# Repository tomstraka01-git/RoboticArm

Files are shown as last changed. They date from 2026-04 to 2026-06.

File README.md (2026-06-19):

# Robotic Arm
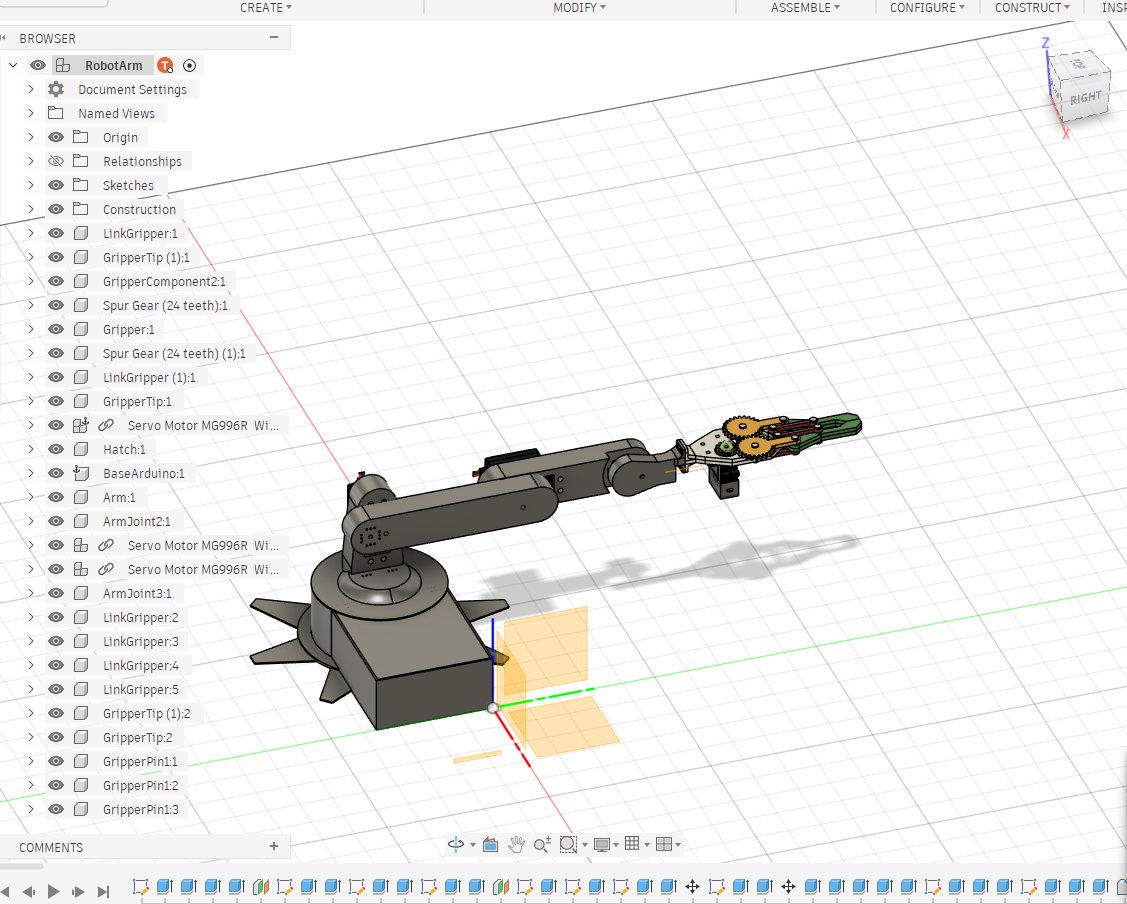
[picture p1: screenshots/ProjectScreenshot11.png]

Robotic arm is a  project about making my own robotic arm from scratch. I designed the arm from scratch and i plan to 3D print the file. Both firmware codes are written by me. The C++ code will run on  microcontroller, i will be using pico 2. The python code can be run on any computer wich can run python files. 

## Operation
First assemble the arm and try to set the servos in 90 degrees position. Then compile the code and wire everything together. After that run the python code and connnect the microcontroller via usb to your computer. Then use the python code to operate it, send signals, set position and record position. The main inverse and forward kinematics run on the pc, the c++ microcontroller code just recieves the serial commands. It uses cosine ease when animating through the listbox to make the movement seems smooth, moves nonlinearly.

### Keybinds
Use keybinds to control the robotic arm easily.
```
[t]: increments the time by 0.5 seconds
[q]: closes the serial port and GUI
[l]: loads animation
[s]: saves animation
[space]: animates smoothly through loaded positions or angles
[r]: records the current position onto the listbox
```
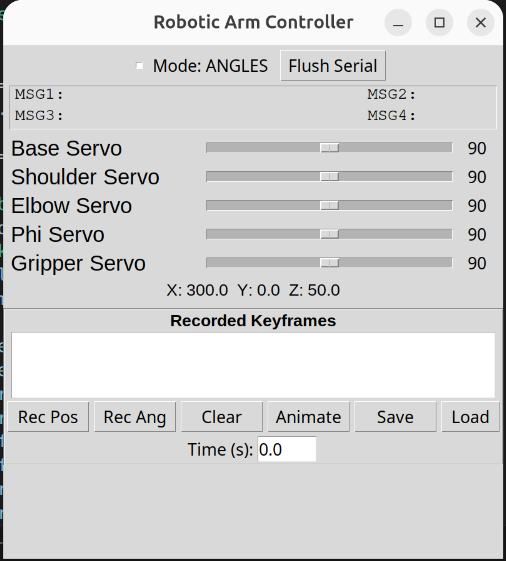
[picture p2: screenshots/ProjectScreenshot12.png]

## What can it do?
You can set positions manually, record and play animations, pick up objects, use it to help you in your everyday life.

## Circuit
The circuit consists of a microcontroller, can be any but i chose pico 2. A PCA9685 servo driver servos, exteral power source and i pcb i will use from my other project. Connect servos to the pcb pins, and connect gnd to gnd and 5V to pcb 5V. Connect signal pins from pcb pins to PCA9685 signal pins. Connect sda scl and power pins from pico 2 to PCA9685. Then upload the code and turn on the power supply. The power supply should be able to handle around 5v 10 amps for safety. The pcb connects the microcontroller, has the adc voltage dividers, output pins for servos, etc. It connects everything together and makes it simplier. It also has some features i am not using like the fans or the adc, but are in the robotic dog project.

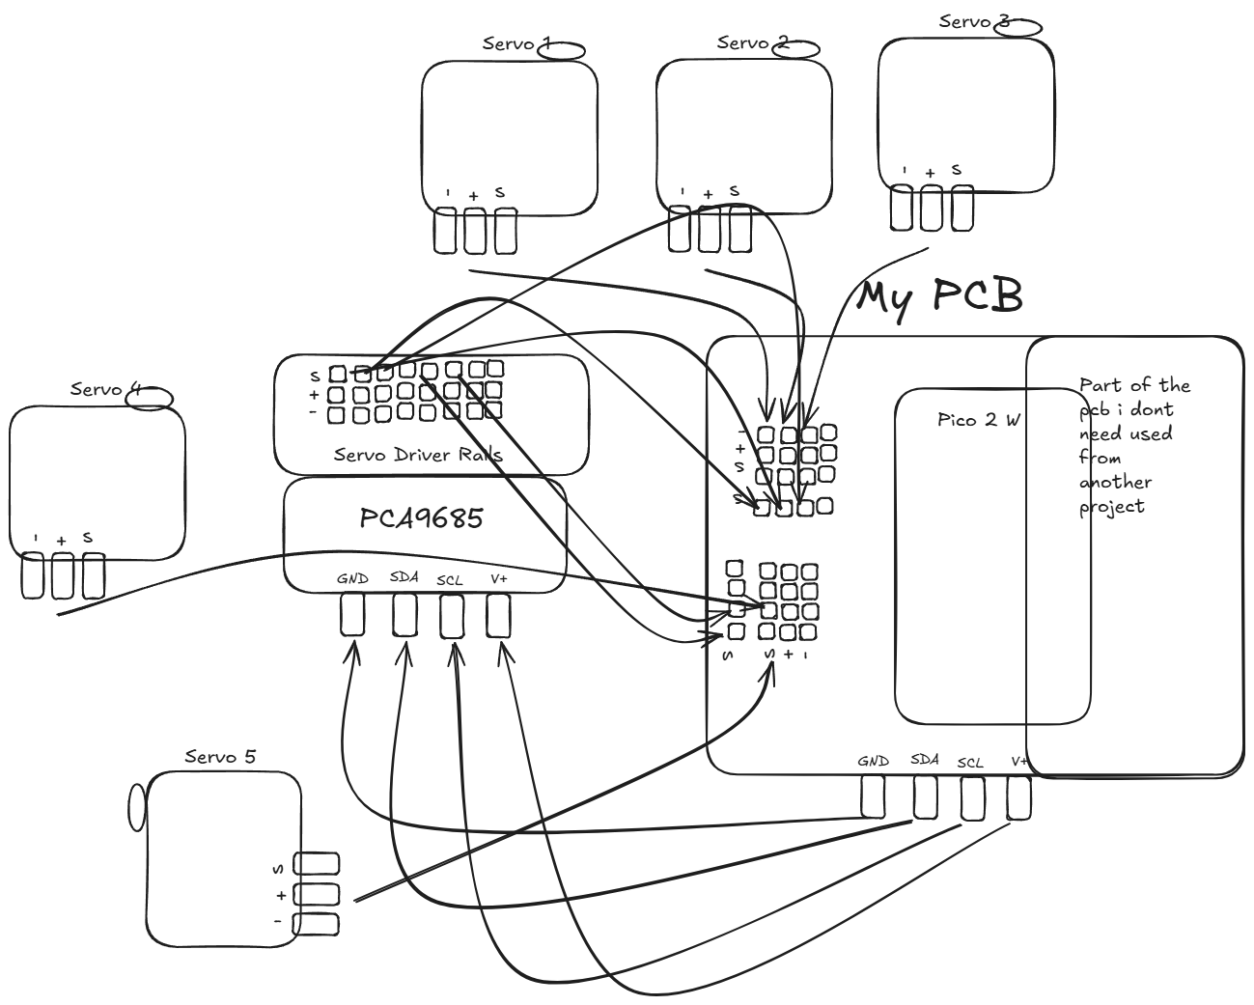
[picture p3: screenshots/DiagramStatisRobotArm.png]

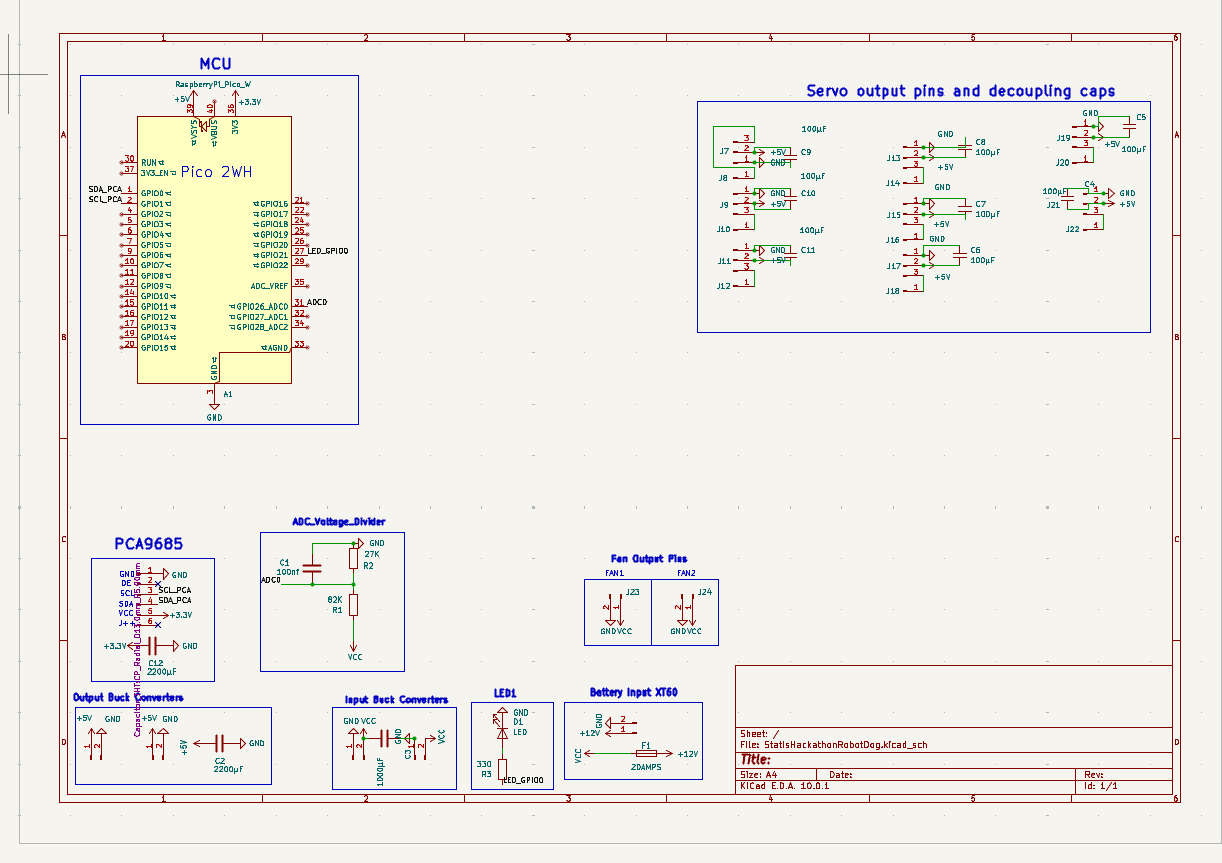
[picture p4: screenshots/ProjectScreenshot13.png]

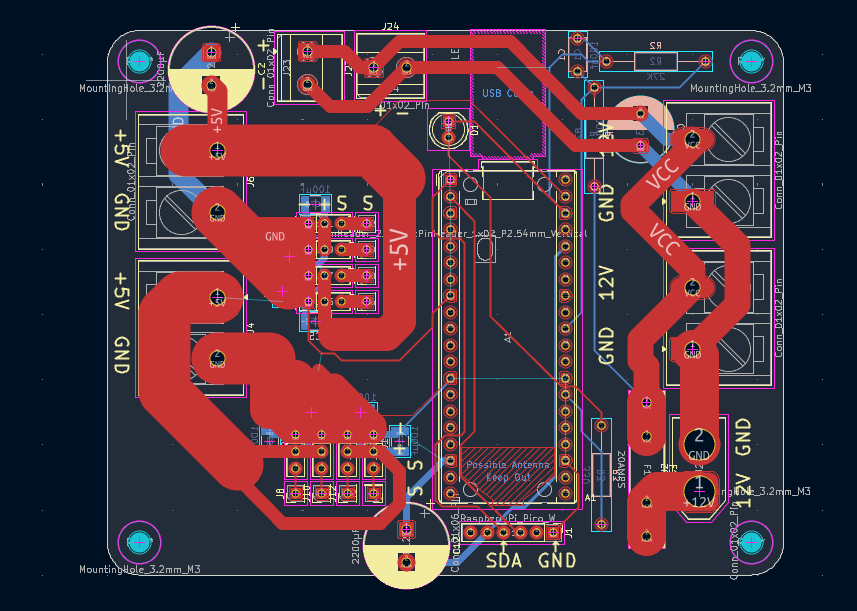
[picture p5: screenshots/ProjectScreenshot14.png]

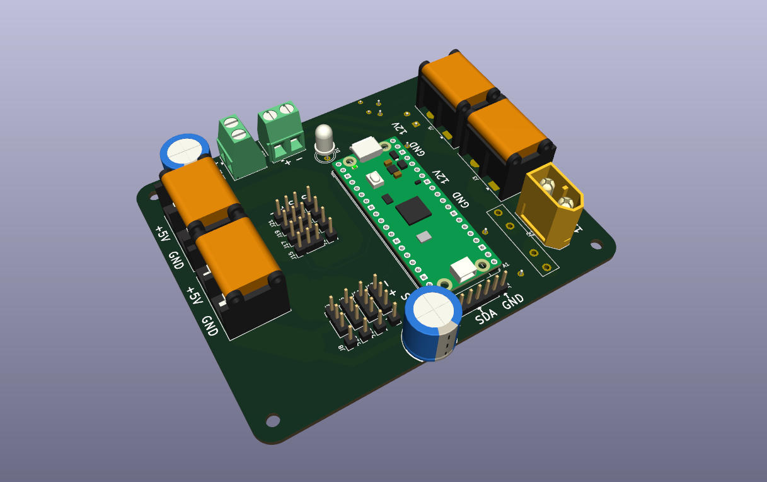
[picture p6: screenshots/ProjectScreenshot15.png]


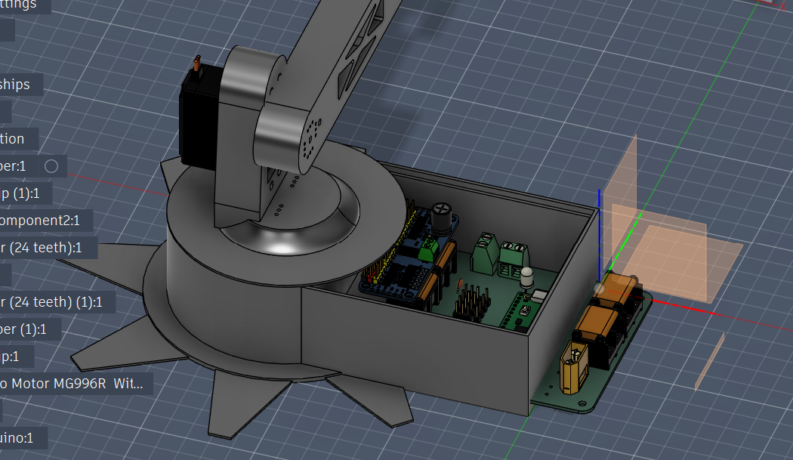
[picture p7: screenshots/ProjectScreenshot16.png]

Here you can see how the pcb will fit into the assembly, the red lines indicate where it will be cut, to save space and remove features from another project i dont need.
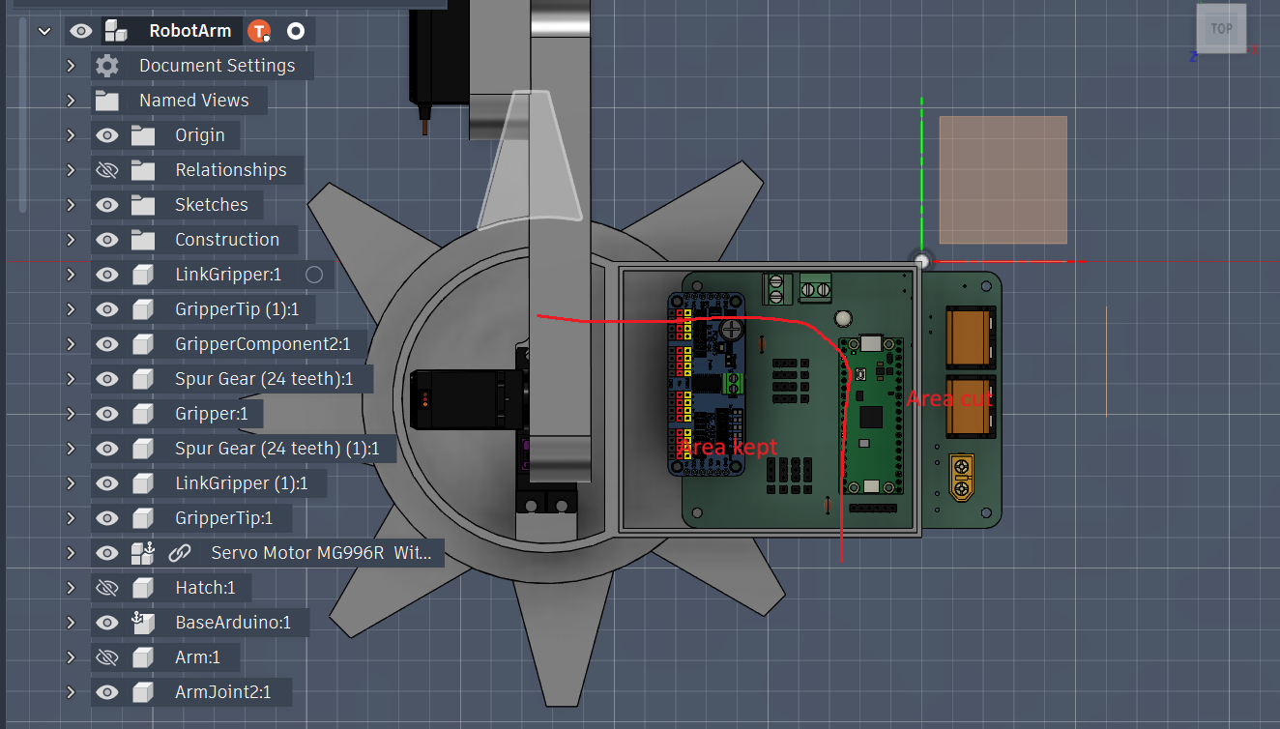
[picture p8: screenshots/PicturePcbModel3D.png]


## How to print?
If you want to replicate the project, you need to buy simillar servos, use some i2c pwm generation module and some circuit to distribute the power. For printing downooad the 3d print file, and use a 3d printer, that has over 400mm print surface. I want to use pla, because it is cheap and okay for my project. You can use other filaments if you want. For my printer, Prusa XL, the slicer says that it would take 22 hours to print and 300 grams to print. Use any microcontroller wich has i2c and serial communication, upload the code and connect it via usb to pc running the python file. Then it should work.

## Why?
Why would i want to build this arm? Because it is a great learning oppurtunity that can teach me many new things. It is also a challange for me, because it is one of my first big projects. I also need a small assistant to help me move things around my desk.



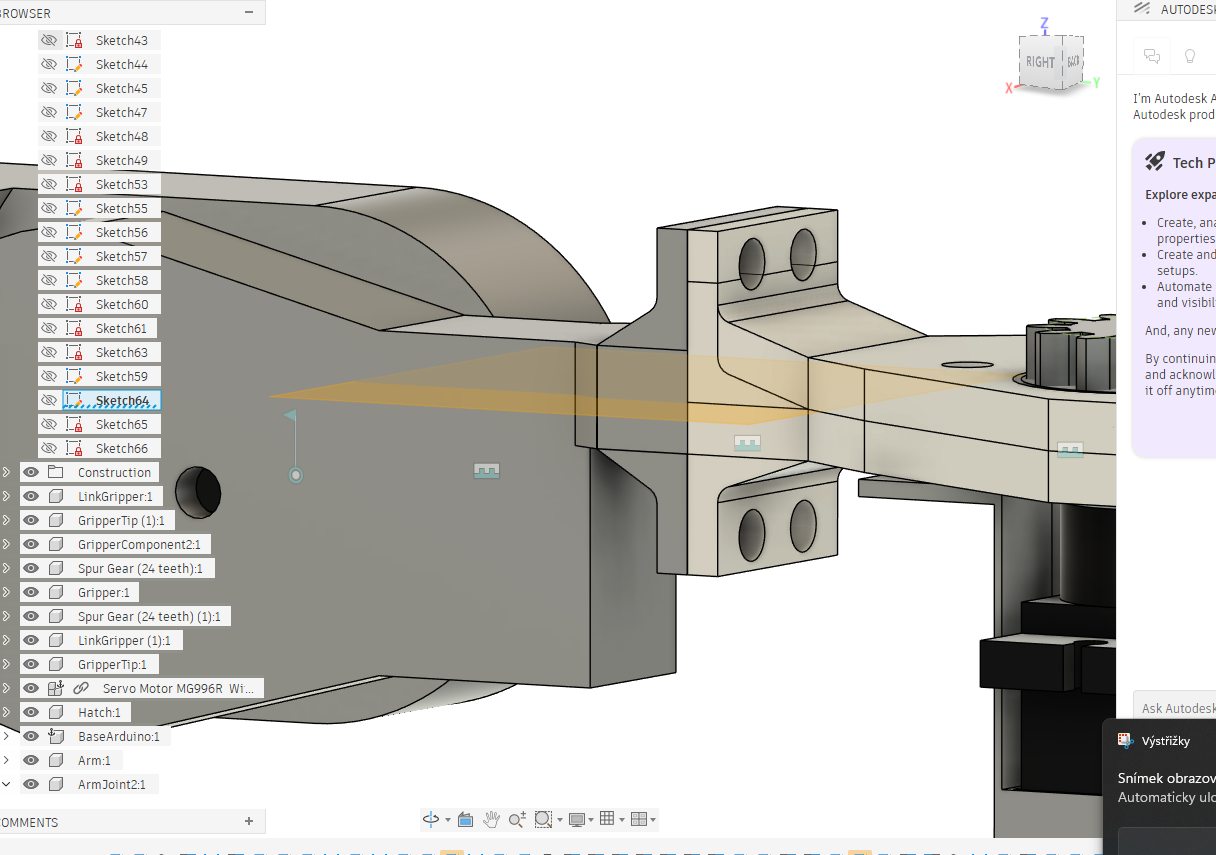
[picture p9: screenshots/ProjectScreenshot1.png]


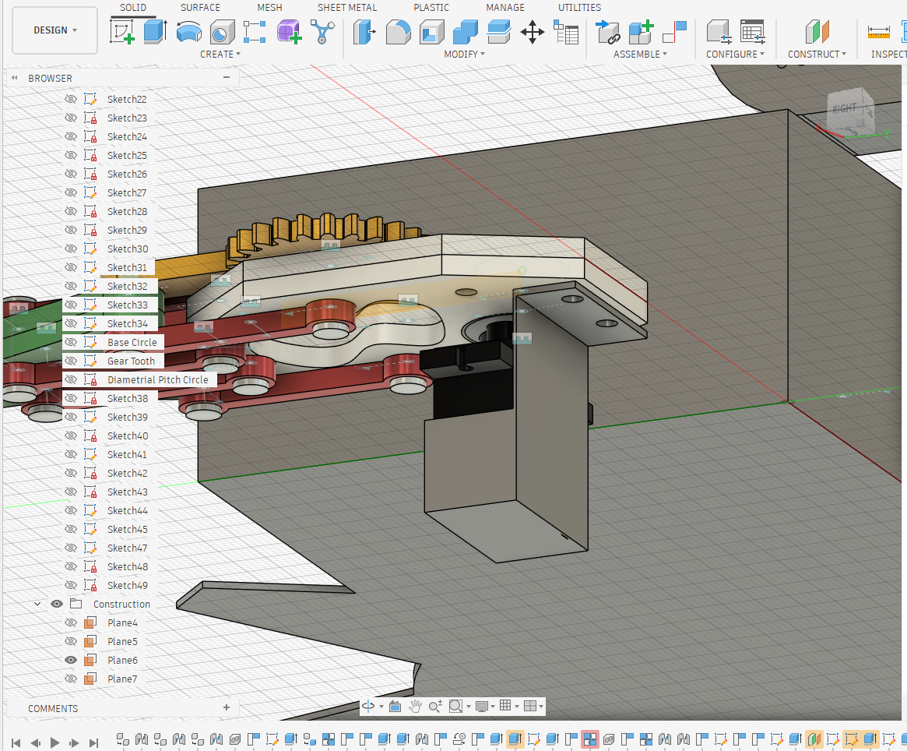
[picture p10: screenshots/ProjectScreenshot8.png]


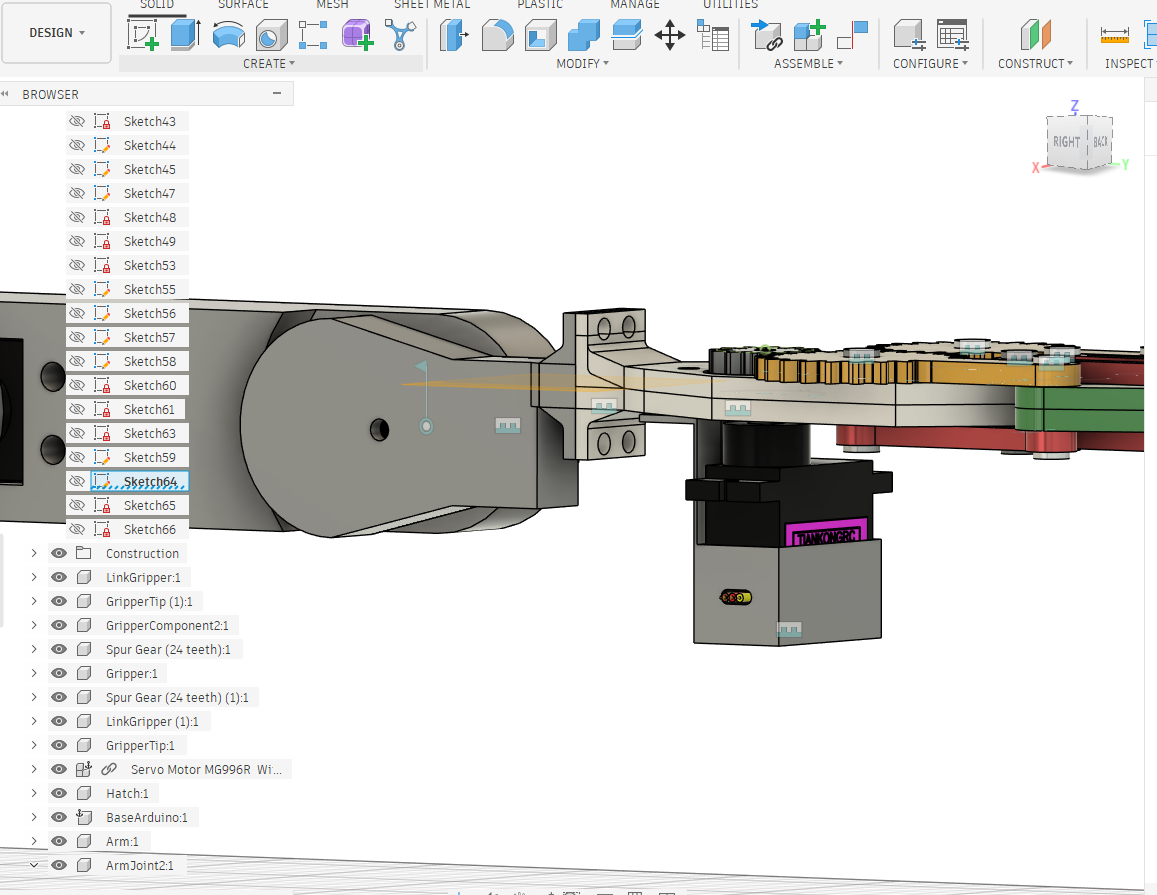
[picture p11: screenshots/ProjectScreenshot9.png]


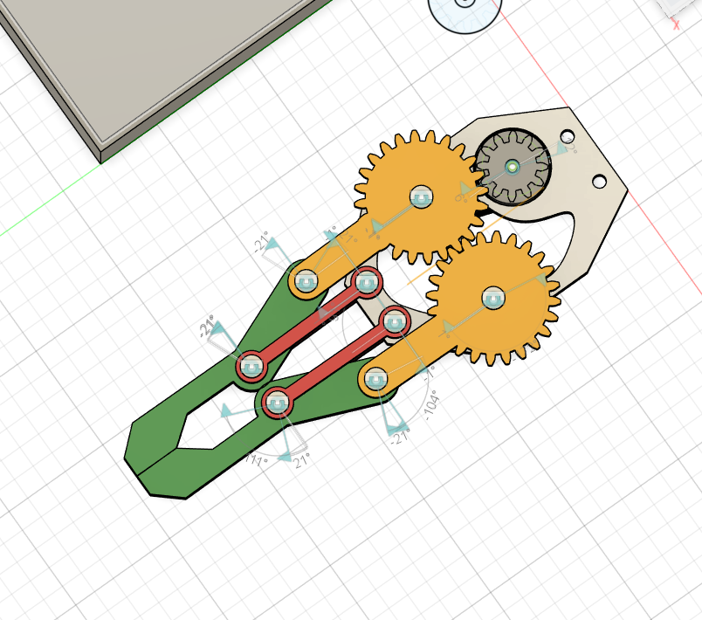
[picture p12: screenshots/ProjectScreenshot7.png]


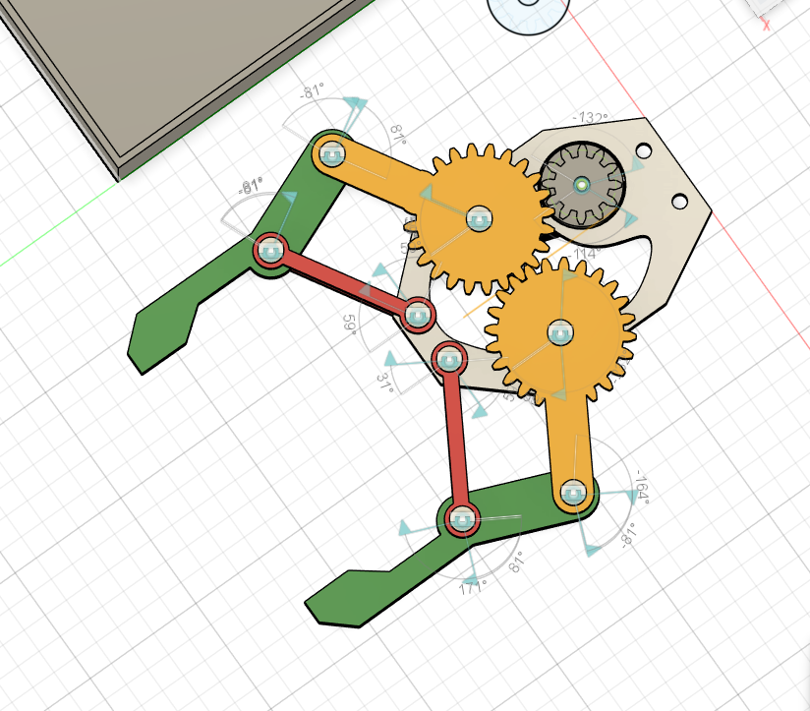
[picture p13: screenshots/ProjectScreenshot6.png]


### Bill of Materials (BOM)

| Name | Purpose | Quantity | Total Cost (USD) | Link | Distributor |
|:---|:---|:---:|:---:|:---|:---|
| Servo 30 cm connector cable extension Male - Female | Cable extension for servo so i can connect it to power and microcontroller when the cable is not long enough to reach it. | 2 | $4.68 | [Link](https://rpishop.cz/servomotory/2878-servo-30-cm-propojka-samec-samice.html) | rpishop.cz |
| Raspberry Pico 2 WH | It is the brain of the robotic arm, will be used to control the servos and if it works compute angles using inverse kynematic for the servos. | 1 | $10.98 | [Link](https://rpishop.cz/590613/raspberry-pico-2-wh/) | rpishop.cz |
| Professional Lab - PLA+ Filament - black(1,75 mm, 1 kg) | It is the filment i will use to print the robotic arm fusion 360 model | 1 | $10.80 | [Link](https://rpishop.cz/616058/professional-lab-pla-plus-cerny/) | rpishop.cz |
| Servo motor MG996R 13 kg, 180° | Motors of the arm, will rotate the joints | 3 | $18.60 | [Link](https://rpishop.cz/641352/servo-mg996r-13-kg/) | rpishop.cz |
| **Total** | | | **$45.06** | | |

Note: PCA9685 I2C driver and power supply were reused from previous projects / already owned, $0 cost.

Made by Tomáš Straka for Statis Hackathon by hackclub.

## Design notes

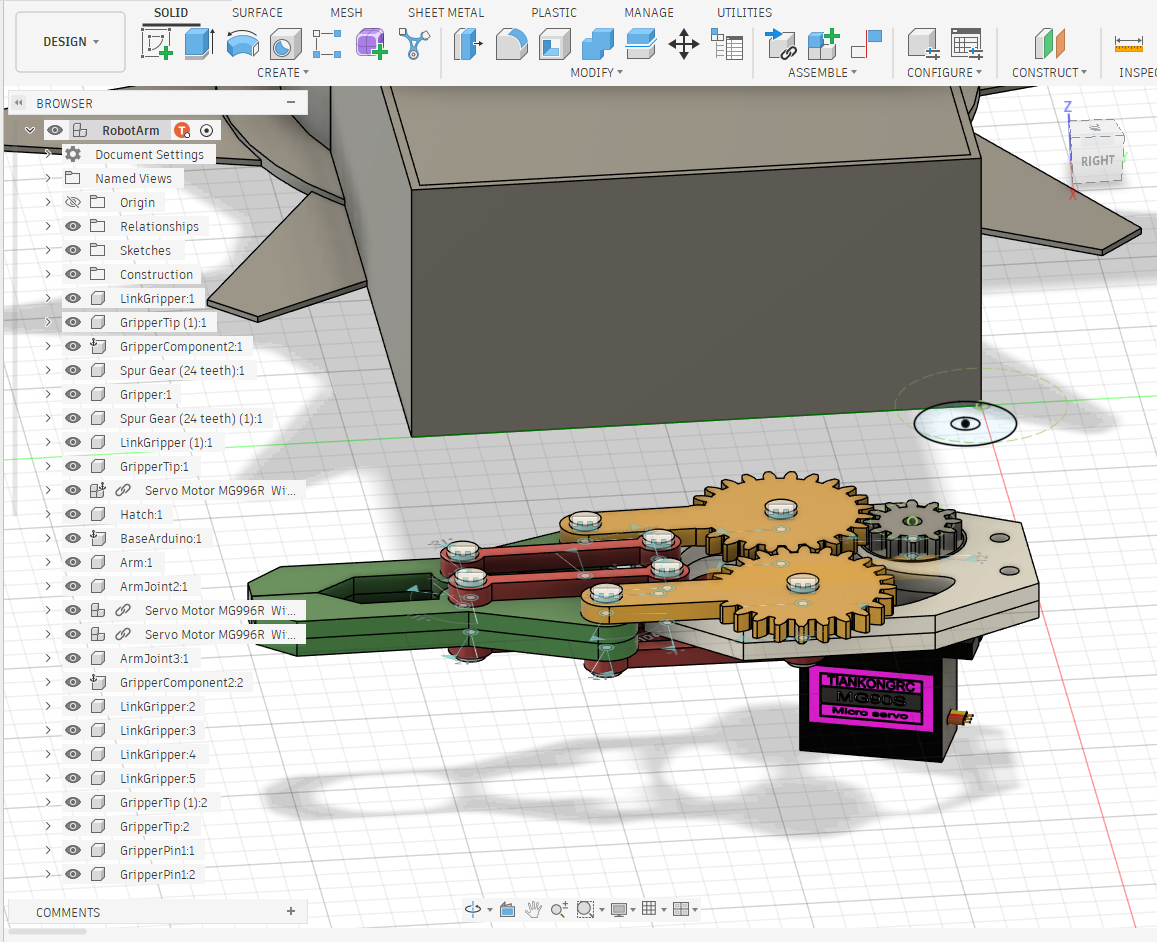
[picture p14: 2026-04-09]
screenshots/ProjectScreenshot5.png

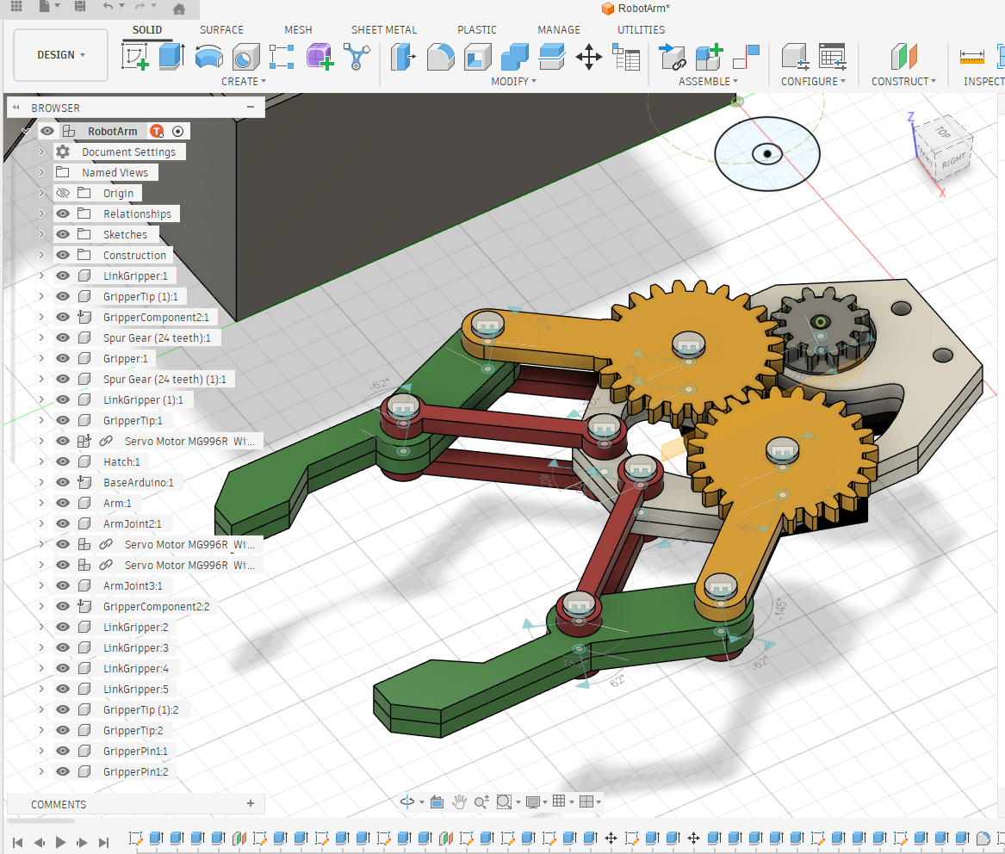
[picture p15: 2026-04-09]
screenshots/ProjectScreenshot4.png

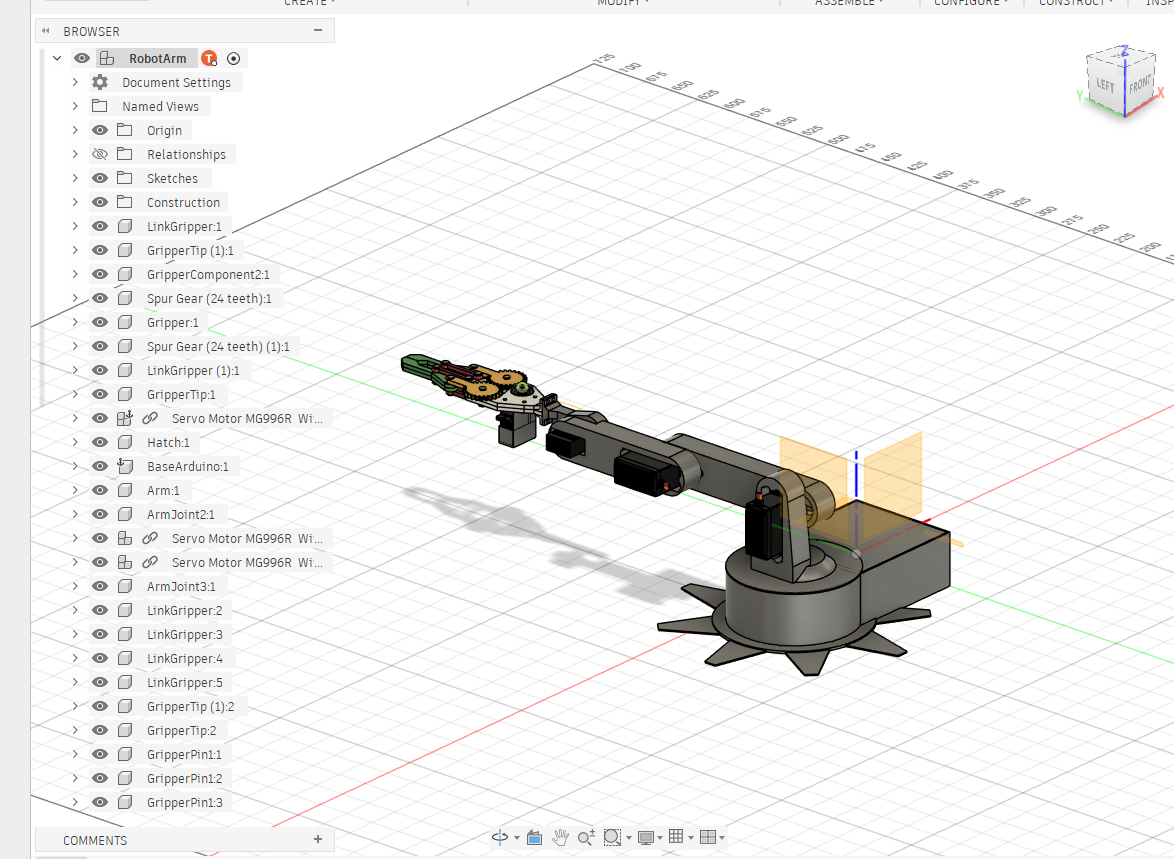
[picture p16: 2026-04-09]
screenshots/ProjectScreenshot10.png

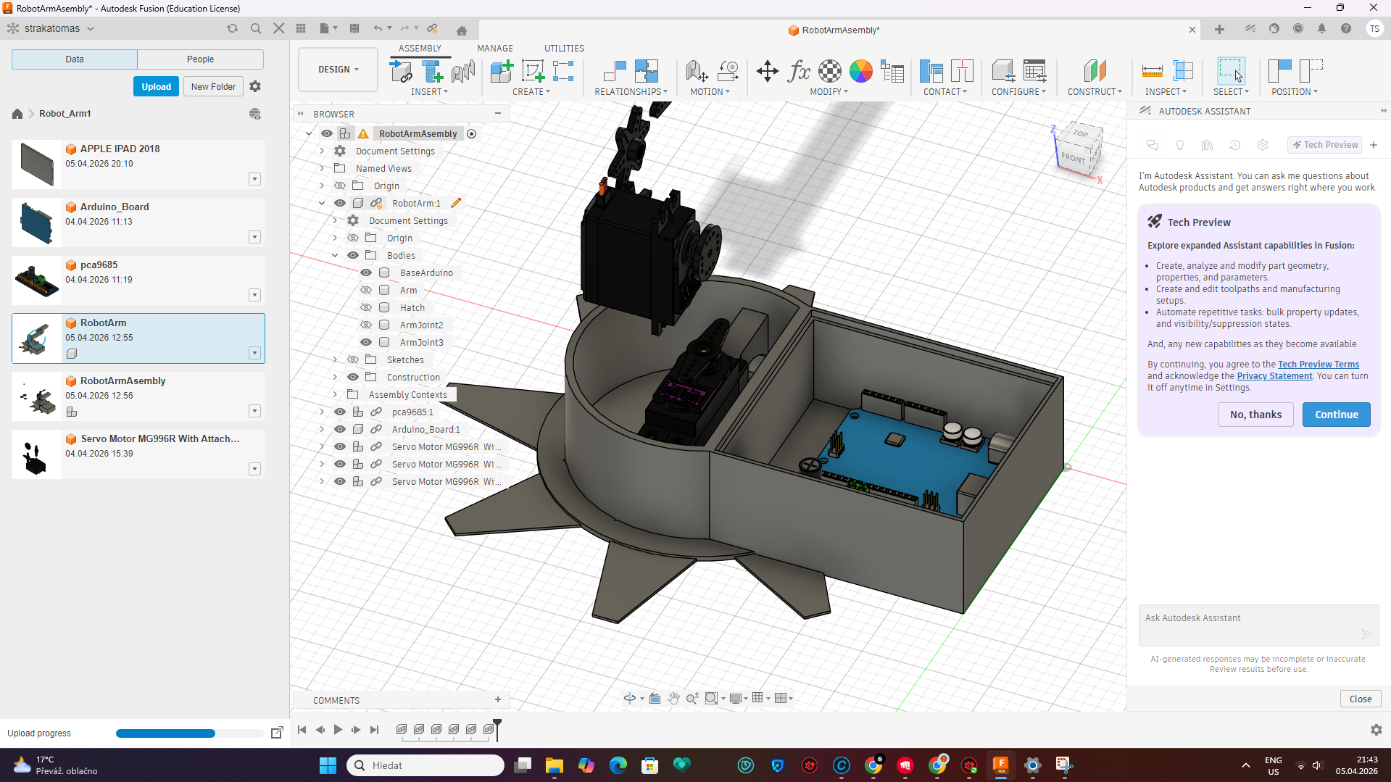
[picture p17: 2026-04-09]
screenshots/ProjectScreenshot3.png

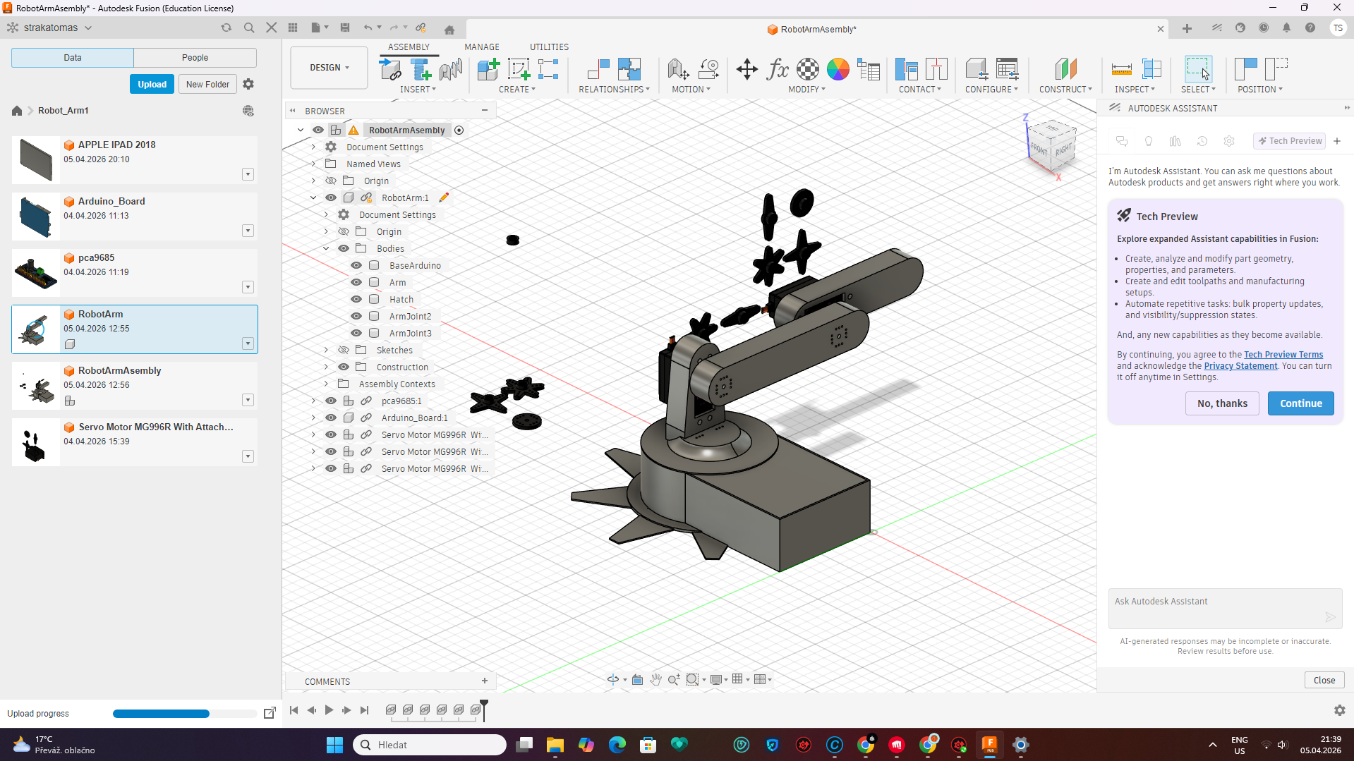
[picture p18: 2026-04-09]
screenshots/ProjectScreenshot2.png

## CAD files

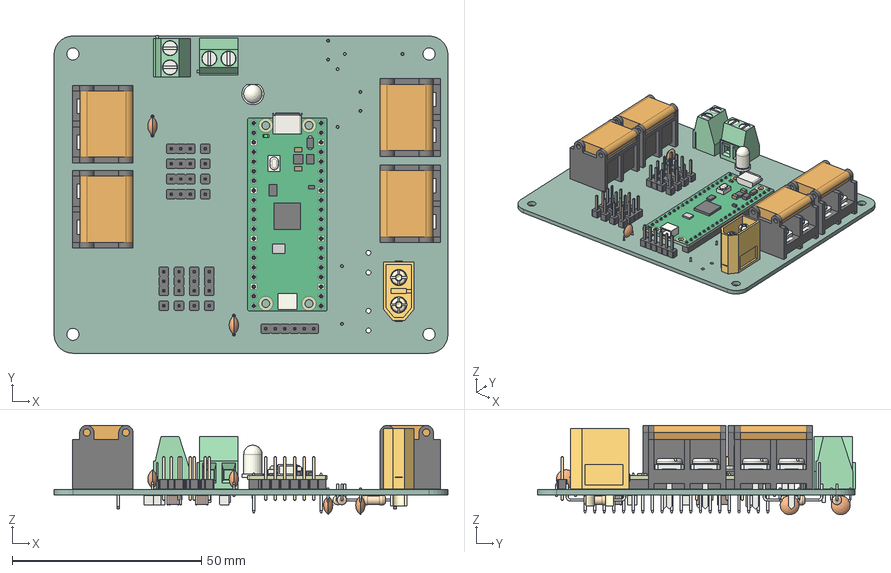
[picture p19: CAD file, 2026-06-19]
boardrobotarm.stp
104.0 x 83.8 x 23.6 mm
PinHeader_1x03_P254mm_Vertical x 8
RaspberryPi_Pico_H_Module_KiCad
RaspberryPi_Pico_Header_DIP-40_H2.54mm_KiCad
XT60 male v9
TerminalBlock_Ningbo-Kagnex_HB9500M_1x02_P9.5mm x 4
C_Disc_D50mm_W25mm_P500mm x 4
PinHeader_1x01_P254mm_Vertical x 8
TerminalBlock_Phoenix_MKDS-1,5-2-5.08_1x02_P5.08mm_Horizontal x 2
PinHeader_1x06_P254mm_Vertical
LED_D5.0mm_Clear
C_1210_3225Metric x 8
R_Axial_DIN0207_L63mm_D25mm_P1524mm_Horizontal x 3
StatisHackathonRobotArm_PCB

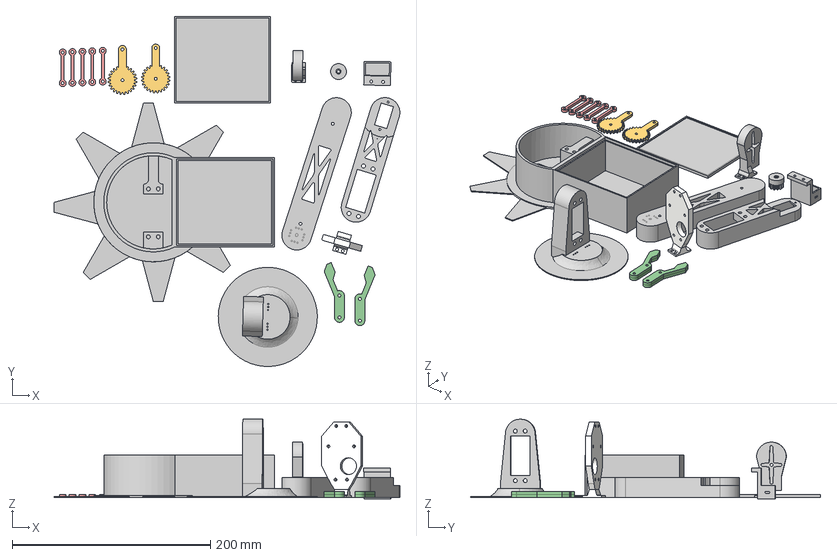
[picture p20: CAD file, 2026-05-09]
RobotArm3DPrint.step
348.7 x 353.0 x 80.3 mm

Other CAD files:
RobotArm3DPrint.stl

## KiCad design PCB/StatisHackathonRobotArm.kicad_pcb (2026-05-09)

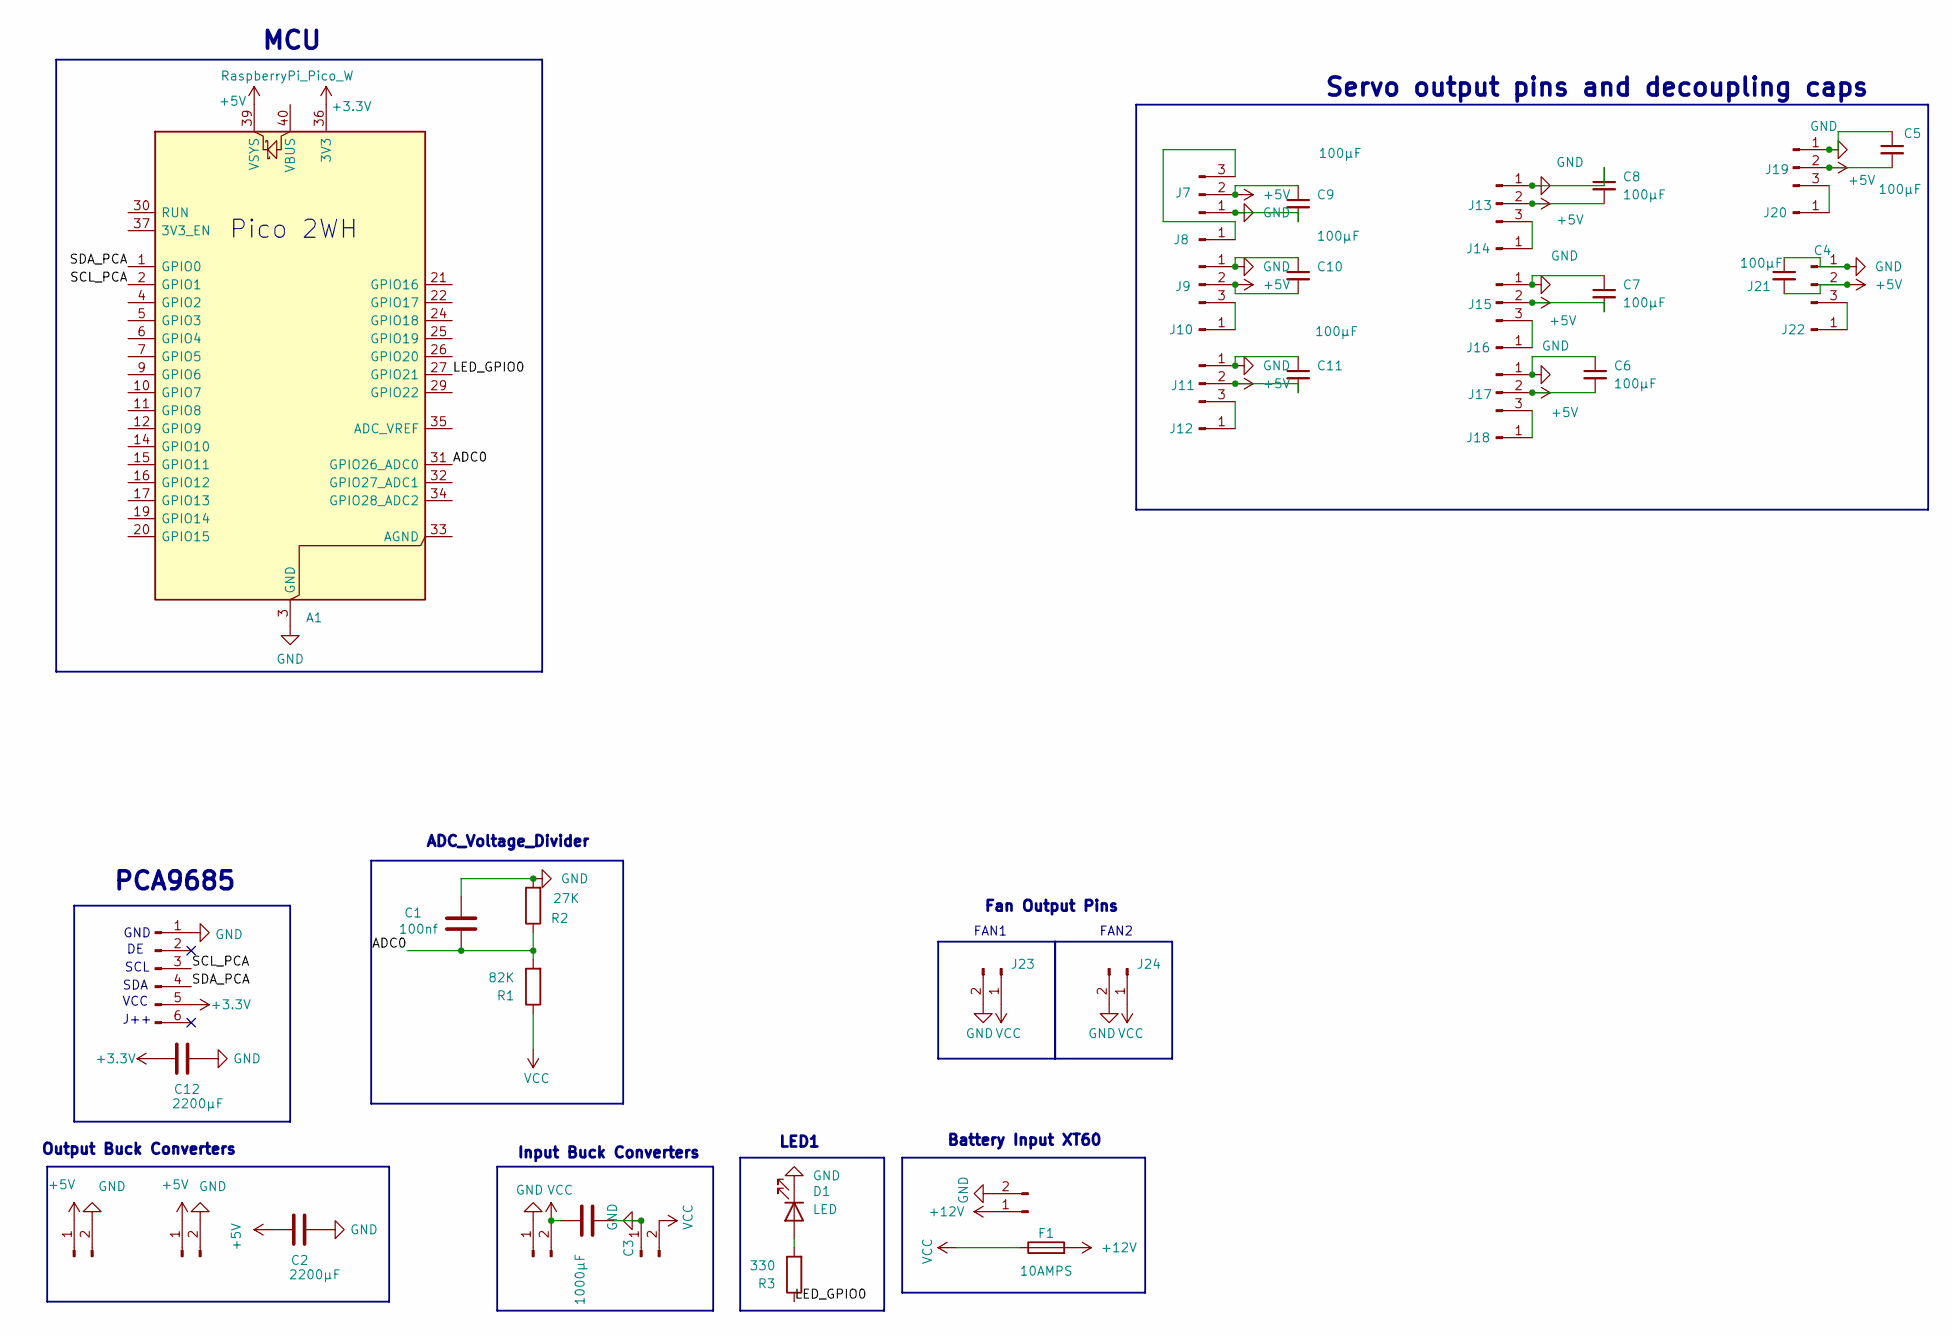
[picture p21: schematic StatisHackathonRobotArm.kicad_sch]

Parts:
A1: RaspberryPi_Pico_W; RaspberryPi_Pico_Common_THT
C1: 100nf; C_Disc_D5.0mm_W2.5mm_P5.00mm
C2, C12: 2200µF; C_Disc_D5.0mm_W2.5mm_P5.00mm
C3: 1000µF; C_Disc_D5.0mm_W2.5mm_P5.00mm
C4, C5, C6, C7, C8, C9, C10, C11: 100µF; C_1210_3225Metric_Pad1.33x2.70mm_HandSolder
D1: LED; LED_D5.0mm_Clear
F1: 10AMPS; Fuseholder_Littelfuse_445_030_series_5x20mm
J1: Conn_01x06_Pin; PinHeader_1x06_P2.54mm_Vertical
J2: Conn_01x02_Pin; AMASS_XT60-M_1x02_P7.20mm_Vertical
J3, J5, J6: Conn_01x02_Pin; TerminalBlock_Ningbo-Kagnex_HB9500M_1x02_P9.5mm
J4: Connector_PinHeader_2.54mm:PinHeader_1x02_P2.54mm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; TerminalBlock_Ningbo-Kagnex_HB9500M_1x02_P9.5mm
J7, J9, J11, J13, J15, J17, J19, J21: Conn_01x03_Pin; PinHeader_1x03_P2.54mm_Vertical
J8, J10, J12, J14, J16, J18, J20, J22: Conn_01x01_Pin; PinHeader_1x01_P2.54mm_Vertical
J23, J24: Conn_01x02_Pin; TerminalBlock_Phoenix_MKDS-1,5-2-5.08_1x02_P5.08mm_Horizont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
R1: 82K; R_Axial_DIN0207_L6.3mm_D2.5mm_P15.24mm_Horizontal
R2: 27K; R_Axial_DIN0207_L6.3mm_D2.5mm_P15.24mm_Horizontal
R3: 330; R_Axial_DIN0207_L6.3mm_D2.5mm_P15.24mm_Horizontal

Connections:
+3.3V: A1.36 (3V3), C12.2, J1.5
+5V: A1.39 (VSYS), C2.2, C4.2, C5.2, C6.2, C7.2, C8.2, C9.1, C10.2, C11.2, J4.1, J6.1, J7.2, J9.2, J11.2, J13.2, J15.2, J17.2, J19.2, J21.2
+12V: F1.2, J2.1
/ADC0: A1.31 (GPIO26_ADC0), C1.2, R1.2, R2.1
/LED_GPIO0: A1.27 (GPIO21), R3.1
/SCL_PCA: A1.2 (GPIO1), J1.3
/SDA_PCA: A1.1 (GPIO0), J1.4
GND: A1.3 (GND), A1.8 (GND), A1.13 (GND), A1.18 (GND), A1.23 (GND), A1.28 (GND), A1.38 (GND), C1.1, C2.1, C3.1, C4.1, C5.1, C6.1, C7.1, C8.1, C9.2, C10.1, C11.1, C12.1, D1.1 (K), J1.1, J2.2, J3.1, J4.2, J5.1, J6.2, J7.1, J9.1, J11.1, J13.1, J15.1, J17.1, J19.1, J21.1, J23.2, J24.2, R2.2
unnamed: D1.2 (A), R3.2
unnamed: J7.3, J8.1 (Pin_1_1)
unnamed: J9.3, J10.1 (Pin_1_1)
unnamed: J11.3, J12.1 (Pin_1_1)
unnamed: J13.3, J14.1 (Pin_1_1)
unnamed: J15.3, J16.1 (Pin_1_1)
unnamed: J17.3, J18.1 (Pin_1_1)
unnamed: J19.3, J20.1 (Pin_1_1)
unnamed: J21.3, J22.1 (Pin_1_1)
VCC: C3.2, F1.1, J3.2, J5.2, J23.1, J24.1, R1.1

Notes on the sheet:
GND
FAN2
Servo output pins and decoupling caps
J++
VCC
Output Buck Converters
Fan Output Pins
Input Buck Converters
SDA
PCA9685
MCU
Battery Input XT60
LED1
SCL
Pico 2WH
FAN1
ADC_Voltage_Divider

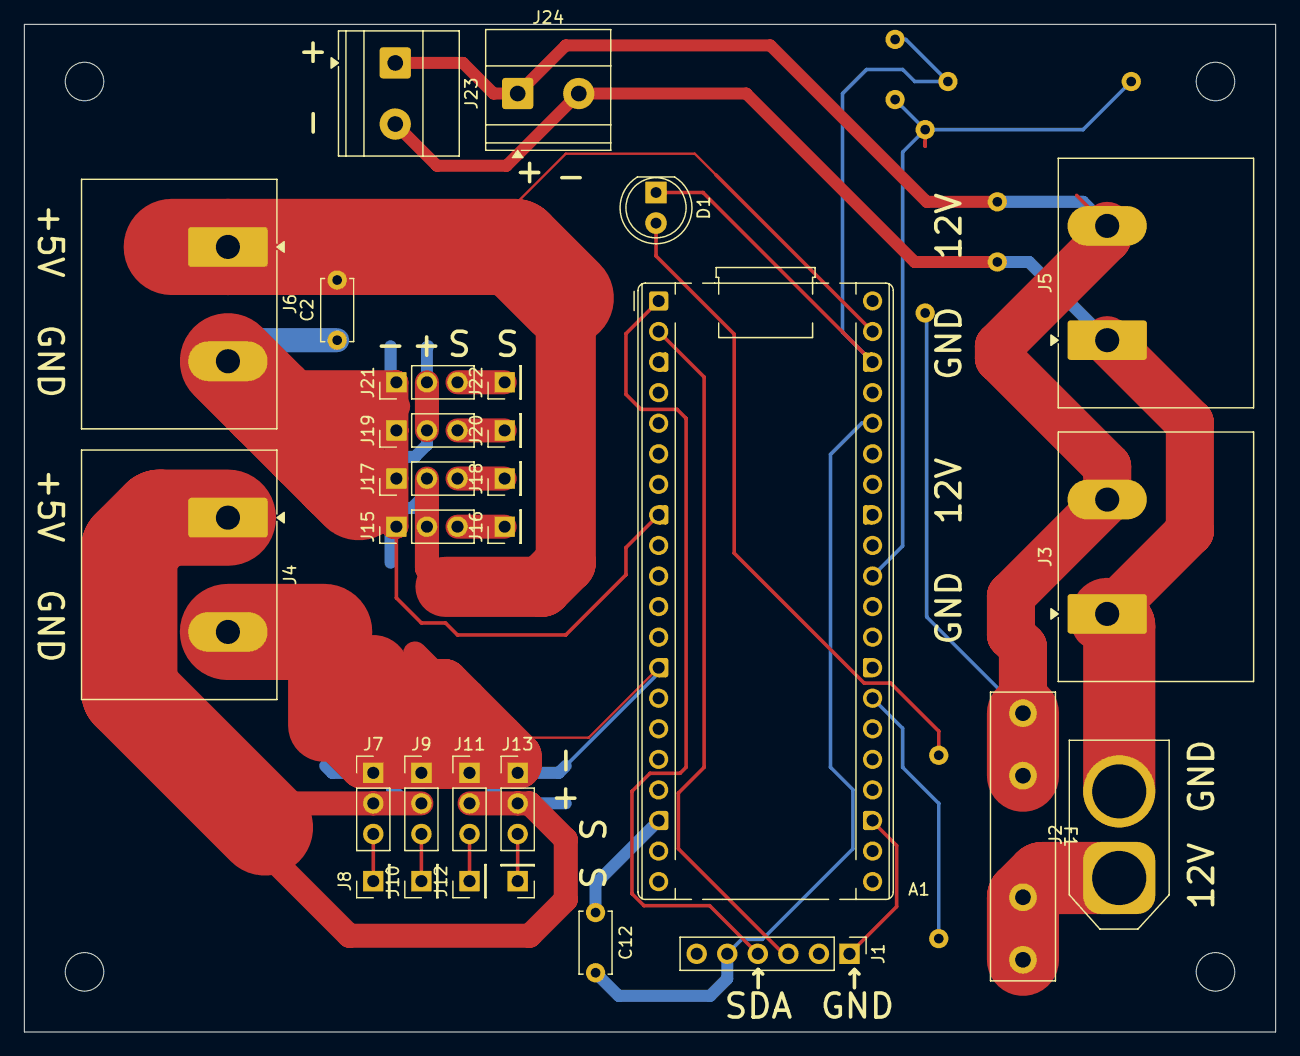
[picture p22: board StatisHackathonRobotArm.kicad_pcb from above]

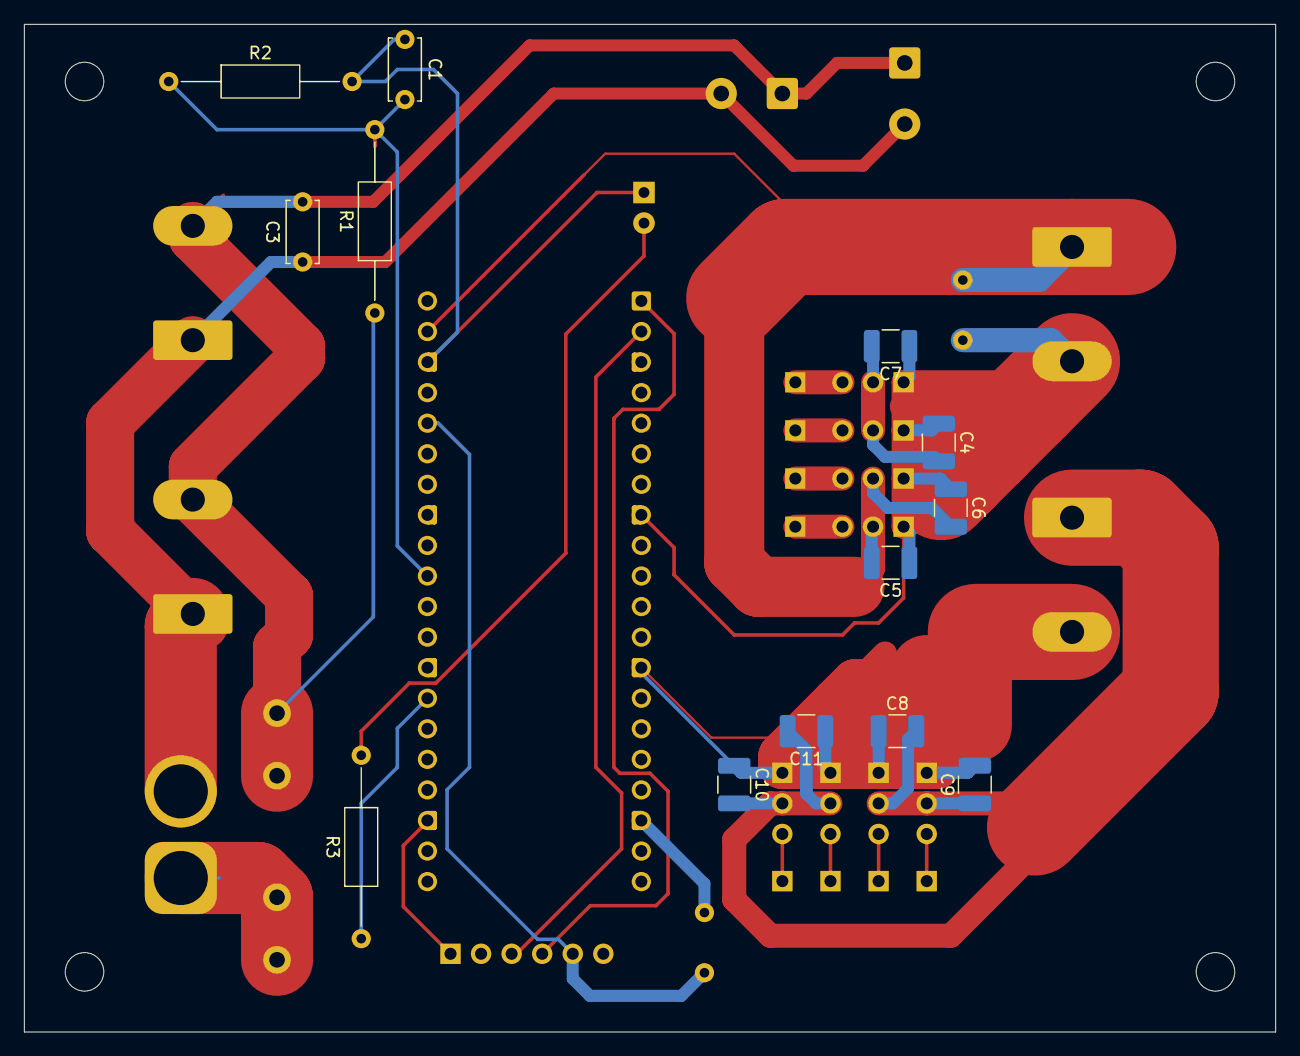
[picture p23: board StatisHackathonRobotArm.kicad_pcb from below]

Board: 2 copper layers, 104.0 x 83.8 mm, 42 parts (13 on the bottom side), 18 nets.

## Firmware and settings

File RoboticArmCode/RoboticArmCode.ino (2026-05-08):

#include <Wire.h>
#include <Adafruit_PWMServoDriver.h>
#include <math.h>

Adafruit_PWMServoDriver pwm = Adafruit_PWMServoDriver(0x40);

#define SERVOMIN  150
#define SERVOMAX  600
#define NUM_SERVOS 5
#define STEP_DELAY 10



int currentAngle[NUM_SERVOS];


struct ServoTarget {
  int target;
  bool moving;
};


ServoTarget servoTargets[NUM_SERVOS];
unsigned long lastStepTime = 0;


int angleToPulse(int angle) {
  return map(angle, 0, 180, SERVOMIN, SERVOMAX);
}

void setServo(uint8_t channel, int angle) {
  angle = constrain(angle, 0, 180);
  pwm.setPWM(channel, 0, angleToPulse(angle));
  currentAngle[channel] = angle;
}

void queueServo(uint8_t channel, int targetAngle) {
  servoTargets[channel].target = constrain(targetAngle, 0, 180);
  servoTargets[channel].moving = true;
}

void updateServos() {
  if (millis() - lastStepTime < STEP_DELAY) return;
  lastStepTime = millis();

  for (int i = 0; i < NUM_SERVOS; i++) {
    if (!servoTargets[i].moving) continue;
    int current = currentAngle[i];
    int target = servoTargets[i].target;
    if (current == target) {
      servoTargets[i].moving = false;
      continue;
    }
    int step = (current < target) ? 1 : -1;
    setServo(i, current + step);
  }
}


void handleSerial() {
  if (!Serial.available()) return;

  String input = Serial.readStringUntil('\n');
  input.trim();


  float values[5] = {0, 0, 0, 0, 0};
  int valueIndex = 0;
  int start = 0;

  for (int i = 0; i <= input.length() && valueIndex < 5; i++) {
    if (i == input.length() || input[i] == ' ') {
      if (i > start) {
        values[valueIndex++] = input.substring(start, i).toFloat();
      }
      start = i + 1;
    }
  }

  if (valueIndex < 5) return; 

  float base = values[0];
  float shoulder = values[1];
  float elbow = values[2];
  float wrist = values[3];
  float gripper = values[4];

  queueServo(0, (int)base);
  queueServo(1, (int)shoulder);
  queueServo(2, (int)elbow);
  queueServo(3, (int)wrist);
  queueServo(4, (int)gripper);
 

  
  Serial.print("Angles => base:"); Serial.print(base);
  Serial.print(" shoulder:"); Serial.print(shoulder);
  Serial.print(" elbow:"); Serial.print(elbow);
  Serial.print(" wrist:"); Serial.print(wrist);
  Serial.print(" gripper:"); Serial.println(gripper);
}

void setup() {
  Serial.begin(115200);
  Wire.begin();
  pwm.begin();
  pwm.setPWMFreq(50);
  delay(500);

  for (int i = 0; i < NUM_SERVOS; i++) {
    currentAngle[i] = 90;
    setServo(i, 90);
    servoTargets[i] = {90, false}; 
  }
}

void loop() {
  handleSerial();
  updateServos();
}

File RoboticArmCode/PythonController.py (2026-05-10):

import tkinter as tk
import serial
import time
import json
import math
from kinematicArm import RobotKinematics, Position

try:
    ser = serial.Serial('COM4', 115200, timeout=1)
    time.sleep(2)
except:
    ser = None

kin = RobotKinematics()
last_send_time = 0
root = tk.Tk()
root.title("Robotic Arm Controller")
root.geometry("800x820")

top_frame = tk.Frame(root)
top_frame.pack(pady=5)
serial_frame = tk.Frame(root, bd=1, relief="sunken")
serial_frame.pack(fill="x", padx=10, pady=2)
content_frame = tk.Frame(root)
content_frame.pack(pady=5)
record_frame = tk.Frame(root, bd=2, relief="groove")
record_frame.pack(pady=5, fill="x")

toggle_state = tk.BooleanVar(value=False)
widgets = []
slider_values = {}
recorded_values_position = []
recorded_values_angle = []
serial_message1 = serial_message2 = serial_message3 = serial_message4 = ""
fk_label_ref = None
last_recorded_time = 0.0
STEPS = 50


def write_serial_values(a, b, c, d, e):
    if ser:
        ser.write(f"{a} {b} {c} {d} {e}\n".encode())

def read_serial_message():
    global serial_message1, serial_message2, serial_message3, serial_message4
    if ser and ser.in_waiting:
        try:
            parts = ser.readline().decode().strip().split(",")
            if len(parts) >= 4:
                serial_message1, serial_message2, serial_message3, serial_message4 = parts[:4]
        except:
            pass
    serial_read_label1.config(text=f"MSG1: {serial_message1}")
    serial_read_label2.config(text=f"MSG2: {serial_message2}")
    serial_read_label3.config(text=f"MSG3: {serial_message3}")
    serial_read_label4.config(text=f"MSG4: {serial_message4}")

def flush_serial():
    global serial_message1, serial_message2, serial_message3, serial_message4
    serial_message1 = serial_message2 = serial_message3 = serial_message4 = ""
    serial_read_label1.config(text="MSG1: ")
    serial_read_label2.config(text="MSG2: ")
    serial_read_label3.config(text="MSG3: ")
    serial_read_label4.config(text="MSG4: ")

def update_fk_label():
    if fk_label_ref is None or toggle_state.get():
        return
    pos = kin.solve_fk(
        slider_values["Base Servo"].get(),
        slider_values["Shoulder Servo"].get(),
        slider_values["Elbow Servo"].get(),
        slider_values["Phi Servo"].get()
    )
    fk_label_ref.config(text=f"X: {pos.x:.1f}  Y: {pos.y:.1f}  Z: {pos.z:.1f}")

def clear_widgets():
    global widgets, fk_label_ref
    for w in widgets:
        w.destroy()
    widgets = []
    fk_label_ref = None

def create_slider(name, ik_mode):
    frame = tk.Frame(content_frame)
    frame.pack(fill="x", padx=10, pady=1)
    tk.Label(frame, text=name, font=("Arial", 13), width=16, anchor="w").pack(side="left")
    var = tk.IntVar(value=100 if ik_mode else 90)
    slider_values[name] = var
    val_label = tk.Label(frame, text=str(var.get()), width=4)
    val_label.pack(side="right")
    last_send = [0]
    def on_slide(val):
        val_label.config(text=val)
        update_fk_label()
        now = time.time()
        if now - last_send[0] > 0.1:
            read_robot_state()
            last_send[0] = now
    slider = tk.Scale(frame, from_=50 if ik_mode else 0, to=200 if ik_mode else 180,
                  orient="horizontal", length=400, variable=var, command=on_slide, showvalue=0)
    slider.pack(side="left", padx=5)
    widgets.append(frame)

def show_position_mode():
    clear_widgets()
    for name in ["X Position", "Y Position", "Z Position", "Phi Angle", "Gripper Servo"]:
        create_slider(name, 1)

def show_angle_mode():
    global fk_label_ref
    clear_widgets()
    for name in ["Base Servo", "Shoulder Servo", "Elbow Servo", "Phi Servo", "Gripper Servo"]:
        create_slider(name, 0)
    fk_label_ref = tk.Label(content_frame, text="FK -> X: -  Y: -  Z: -", font=("Arial", 10))
    fk_label_ref.pack(pady=2)
    widgets.append(fk_label_ref)
    update_fk_label()

def update_mode():
    if toggle_state.get():
        toggle_button.config(text="Mode: POSITION")
        show_position_mode()
    else:
        toggle_button.config(text="Mode: ANGLES")
        show_angle_mode()

def record_position():
    global last_recorded_time
    if not toggle_state.get():
        return
    t = float(time_input.get())
    if t < last_recorded_time:
        time_input_label.config(text=f"t >= {last_recorded_time}")
        return
    last_recorded_time = t
    x, y, z = slider_values["X Position"].get(), slider_values["Y Position"].get(), slider_values["Z Position"].get()
    phi, grip = slider_values["Phi Angle"].get(), slider_values["Gripper Servo"].get()
    recorded_values_position.append((x, y, z, phi, grip, t))
    record_listbox.insert(tk.END, f"X:{x} Y:{y} Z:{z} P:{phi} G:{grip} T:{t}")

def record_angles():
    global last_recorded_time
    if toggle_state.get():
        return
    t = float(time_input.get())
    if t < last_recorded_time:
        time_input_label.config(text=f"t >= {last_recorded_time}")
        return
    last_recorded_time = t
    b = slider_values["Base Servo"].get()
    s = slider_values["Shoulder Servo"].get()
    e = slider_values["Elbow Servo"].get()
    p = slider_values["Phi Servo"].get()
    g = slider_values["Gripper Servo"].get()
    recorded_values_angle.append((b, s, e, p, g, t))
    record_listbox.insert(tk.END, f"B:{b} S:{s} E:{e} P:{p} G:{g} T:{t}")

def clear_records():
    global last_recorded_time
    recorded_values_position.clear()
    recorded_values_angle.clear()
    record_listbox.delete(0, tk.END)
    last_recorded_time = 0.0

def save_animation():
    data = {"mode": "ik", "sequence": recorded_values_position} if toggle_state.get() \
           else {"mode": "angles", "sequence": recorded_values_angle}
    with open("animation.json", "w") as f:
        json.dump(data, f, indent=4)
    print("Animation saved")

def load_animation():
    global recorded_values_position, recorded_values_angle, last_recorded_time
    try:
        with open("animation.json", "r") as f:
            data = json.load(f)
    except FileNotFoundError:
        print("No saved animation found")
        return
    record_listbox.delete(0, tk.END)
    last_recorded_time = 0.0
    if data["mode"] == "ik":
        recorded_values_position = [tuple(kf) for kf in data["sequence"]]
        toggle_state.set(True)
        update_mode()
        for x, y, z, phi, grip, t in recorded_values_position:
            record_listbox.insert(tk.END, f"X:{x} Y:{y} Z:{z} P:{phi} G:{grip} T:{t}")
    else:
        recorded_values_angle = [tuple(kf) for kf in data["sequence"]]
        toggle_state.set(False)
        update_mode()
        for b, s, e, p, g, t in recorded_values_angle:
            record_listbox.insert(tk.END, f"B:{b} S:{s} E:{e} P:{p} G:{g} T:{t}")
    print("Animation loaded")

def cosine_ease(a, b, t):
    return a + (b - a) * (1 - math.cos(t * math.pi)) / 2
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

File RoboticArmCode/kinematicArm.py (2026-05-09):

import math
from dataclasses import dataclass
from typing import Optional


@dataclass
class Position:
    x: float
    y: float
    z: float


class RobotKinematics:


    """
        from kinematics import RobotKinematics, Position

        kin = RobotKinematics()

        # Inverse kinematics
        angles = kin.solve_ik(x=100, y=0, z=80, phi_deg=90)
        if angles:
            base, shoulder, elbow, wrist = angles

        # Forward kinematics
        pos = kin.solve_fk(base=90, shoulder=90, elbow=90, wrist=90)
        print(pos.x, pos.y, pos.z)
    """

    def __init__(
        self,
        H0: float = 50.0,
        L1: float = 105.0,
        L2: float = 100.0,
        L3: float = 35.0,
        Lg: float = 60.0,
    ):

        self.H0 = H0
        self.L1 = L1
        self.L2 = L2
        self.L3 = L3
        self.Lg = Lg

    def solve_fk(
        self,
        base: float,
        shoulder: float,
        elbow: float,
        wrist: float,
    ) -> Position:
        

        t0 = math.radians(base - 90)
        t1 = math.radians(shoulder - 90)
        t2 = math.radians(elbow - 90)
        t3 = math.radians(wrist - 90)
        phi = t1 + t2 + t3

        r = (
            self.L1 * math.cos(t1)
            + self.L2 * math.cos(t1 + t2)
            + (self.L3 + self.Lg) * math.cos(phi)
        )
        z = (
            self.H0
            + self.L1 * math.sin(t1)
            + self.L2 * math.sin(t1 + t2)
            + (self.L3 + self.Lg) * math.sin(phi)
        )

        return Position(
            x=r * math.cos(t0),
            y=r * math.sin(t0),
            z=z,
        )

    def solve_ik(self, x, y, z, phi_deg=0.0):
        phi = math.radians(phi_deg - 90.0)
        theta0 = math.atan2(y, x)

        r = math.sqrt(x**2 + y**2) - self.L3 * math.cos(phi)
        zw = z - self.H0 - self.L3 * math.sin(phi)
        r -= self.Lg * math.cos(phi)
        zw -= self.Lg * math.sin(phi)

        dist = math.sqrt(r**2 + zw**2)
        if dist > (self.L1 + self.L2) or dist < abs(self.L1 - self.L2):
            return None

        cos_theta2 = (r**2 + zw**2 - self.L1**2 - self.L2**2) / (2.0 * self.L1 * self.L2)
        cos_theta2 = max(-1.0, min(1.0, cos_theta2))
        theta2 = math.acos(cos_theta2)  

        k1 = self.L1 + self.L2 * math.cos(theta2)
        k2 = self.L2 * math.sin(theta2)
        theta1 = math.atan2(zw, r) - math.atan2(k2, k1)
        theta3 = phi - (theta1 + theta2)

        base = self._clamp(int(math.degrees(theta0) + 90))
        shoulder = self._clamp(int(math.degrees(theta1) + 90))
        elbow = self._clamp(int(math.degrees(theta2) + 90))  
        wrist = self._clamp(int(math.degrees(theta3) + 90))

        return base, shoulder, elbow, wrist


    @staticmethod
    def _clamp(angle: int, lo: int = 0, hi: int = 180) -> int:
        return max(lo, min(hi, angle))

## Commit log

2026-05-08 added 3d print file, changed code, tried migrating from microcontroller kinematics to pc ones, still not done
    [RobotArm3DPrint.stl]
2026-05-09 changed code and added fotos
    [RobotArm.step, RobotArm3DPrint.step, StatisHackathonRobotDog.kicad_pcb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]
2026-05-09 changed robotic arm code little
2026-06-01 added photos, changed file names, added gerbers
    [StatisHackathonRobotArm.kicad_pcb, StatisHackathonRobotArm.kicad_sch]
2026-06-01 added 3d model of the pcb
2026-06-19 added pcb model to the main 3D model
    [RobotArm.step, boardrobotarm.stp]
